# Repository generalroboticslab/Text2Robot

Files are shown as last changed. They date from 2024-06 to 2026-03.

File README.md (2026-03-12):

# Text2Robot

Ryan Ringel,
[Zachary Charlick](https://zacharycharlick.com),
[Jiaxun Liu](https://jiaxunliu.com),
Boxi Xia,
[Boyuan Chen](http://boyuanchen.com/)
<br>
Duke University
<br>

### [Project Website](http://www.generalroboticslab.com/blogs/blog/2024-06-28-text2robot/index.html) | [Video](https://www.youtube.com/watch?v=Cwq7G6OUeGg) | [Paper](https://arxiv.org/abs/2406.19963)

## Overview
This repo contains the Fusion360 and Python implementation for paper "Text2Robot." Our pipeline automatically converts a text prompt to a quadrupedal robot. We utilize a state of the art text to mesh generative model as initialization for our pipeline, and convert the static mesh to a kinetic robot model. We evolve the robots control and morphology simultaneously using our evolutionary algorithm.

<p align="center">
    teaser
</p>

## Citation

If you find our paper or codebase helpful, please consider citing:

```
@article{ringel2024text2robot,
      title={Text2Robot: Evolutionary Robot Design from Text Descriptions}, 
      author={Ryan P. Ringel and Zachary S. Charlick and Jiaxun Liu and Boxi Xia and Boyuan Chen},
      year={2024},
      eprint={2406.19963},
      archivePrefix={arXiv},
      primaryClass={cs.RO},
      url={https://arxiv.org/abs/2406.19963}, 
}
```

## Content

- [Installation](#installation)
- [Text2Mesh](#text2mesh)
- [Mesh2CAD](#mesh2cad)
- [CAD2URDF](#cad2urdf)
- [Evolutionary Loop](#evolutionary-loop)
- [Sim2Real](#sim2real)

## Project Structure
```
├── conda_env_py38.yaml                     # Conda enviornment for isaacgym
├── Assembly Instructions.pdf               # Instructions for print and assembly of bots
├── Evolutionary_Algorithm
│   ├── driver.py                           # Evolutionary algo driver
│   ├── Example_Frog_Experiment             # Example Experiment URDF_Bank and directory
│   ├── experiments                         # Customize command line overrides for your experiment
│   ├── extract_rewards_from_tensorboard_file.py
│   ├── gen_config_file.py
│   ├── greatest_reward.py
│   ├── init_population.py
│   ├── __init__.py
│   ├── output
│   ├── __pycache__
│   ├── swapping.py
│   ├── train_util.py
│   └── util.py
├── Fusion360_Scripts                               
│   ├── Install_Packages                   # Install necessary python packages for Fusion360
│   └── Wrapper                            # Mesh to Robot Model(s) w/ geometric slicing
├── __init__.py
├── legged_env
│   ├── assets
│   ├── envs                               # Navigate here for visualization & sim2real
│   ├── __init__.py
│   ├── __pycache__
│   └── README.md
├── README.md
├── Sim2Real                               # Sim2Real receiver for RaspPi
│   └── receiver.py
└── STL_Files                              # Example Text-to-mesh and modular components
    ├── Electronics_Modules
    └── Example_Meshes
```
## Installation

The installation has been tested on Ubuntu 22.04.4 LTS with CUDA 12.3. The experiments are performed on several different servers with either PNY RTX A6000, NVIDIA GeForce RTX 3090, or NVIDIA A100 PCIe GPUs.

The conda yaml file `conda_env_py38.yaml` can be found in the base folder of the repo

```bash
alias conda="micromamba"

# Create environment
conda env create --file conda_env_py38.yaml -y

# Activate the environment
conda activate py38

# Export library path
export LD_LIBRARY_PATH=${CONDA_PREFIX}/lib
```

For Fusion360 geometric slicing installation, see section [Mesh2CAD](#mesh2cad)

## Text2Mesh
We use the Meshy website https://www.meshy.ai/ to generate STL meshes from text prompts. STL's used in our experiments are provided in `STL_Files/Example_Meshes`. 

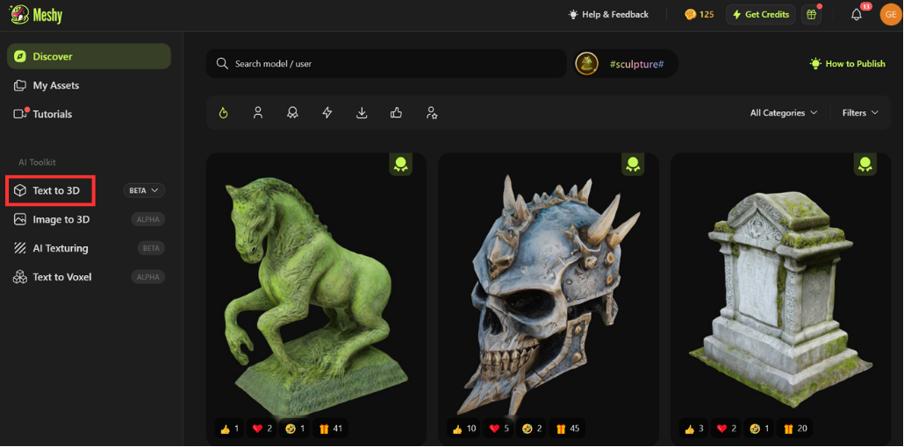
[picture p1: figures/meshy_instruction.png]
MeshyHomeScreen


Additional meshes can be generated using Meshy, although they are not guaranteed to work with the provided slicing script. Include the keywords "quadrupedal walking robot" in the text prompt for best results.

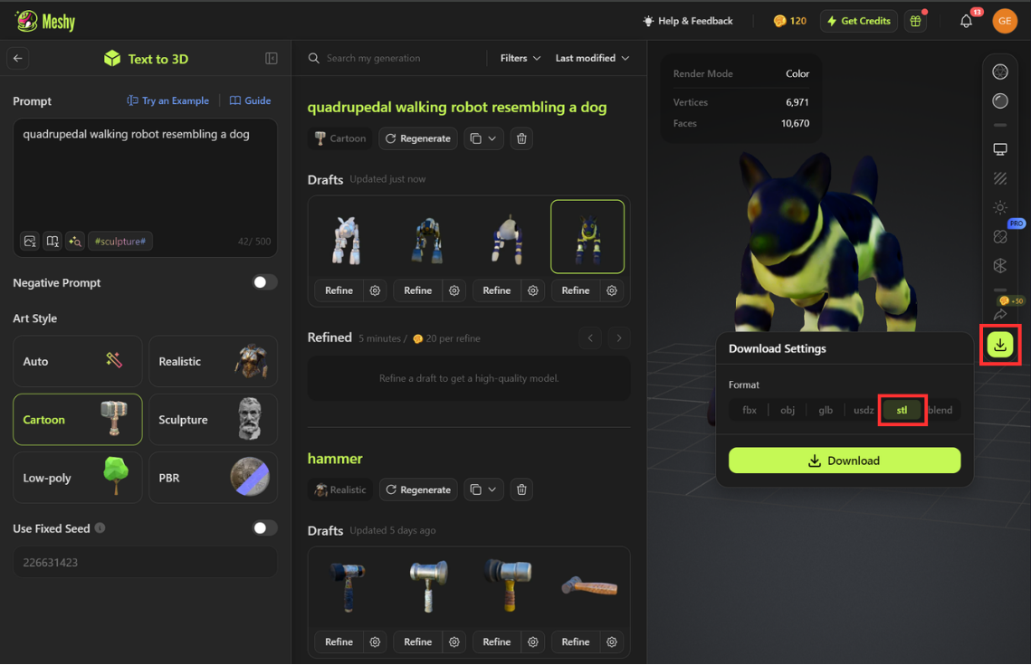
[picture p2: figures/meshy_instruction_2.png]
MeshyText


## Mesh2CAD

STL meshes can be converted to a fusion360 assembly using the provided sliceBody script. First open Fusion360, and preprocess the generated or downloaded mesh desired. Installation instructions can be found at https://www.autodesk.com/campaigns/education/fusion-360. Insert the mesh into a fusion360 document, and use the convert mesh operation to convert the mesh to a brepboy. Organic mesh conversion is enabled with the fusion design extension.

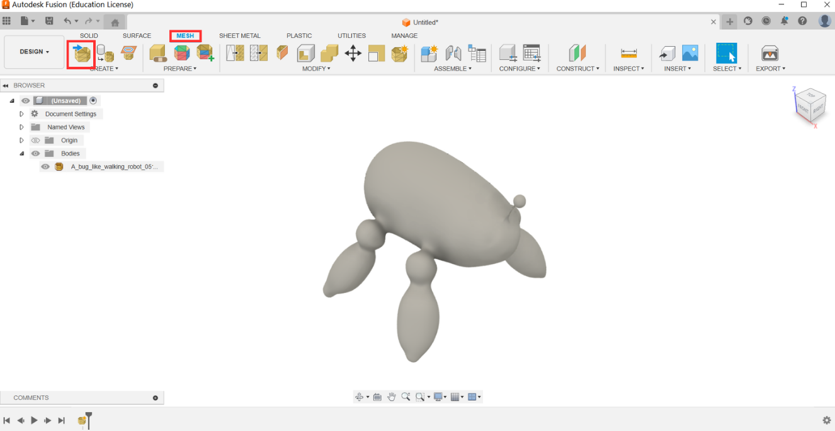
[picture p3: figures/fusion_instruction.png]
InsertMesh

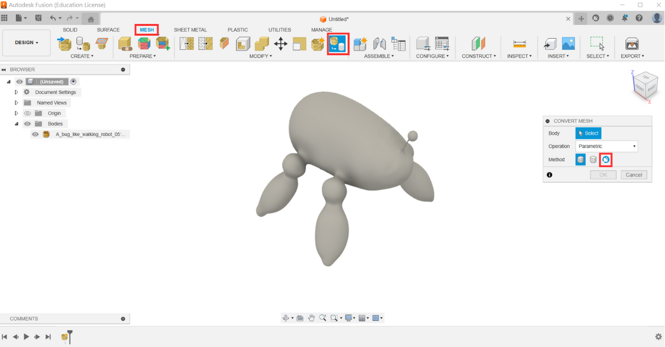
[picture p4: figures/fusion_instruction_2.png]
ConvertMesh


To slice the brepbody, add both python scripts in the 'Fusion360_Scripts' folder into Fusion360. To link an add-in in Fusion360, click on the green plus, and navigate to and select the Wrapper and Install_Packages folders.

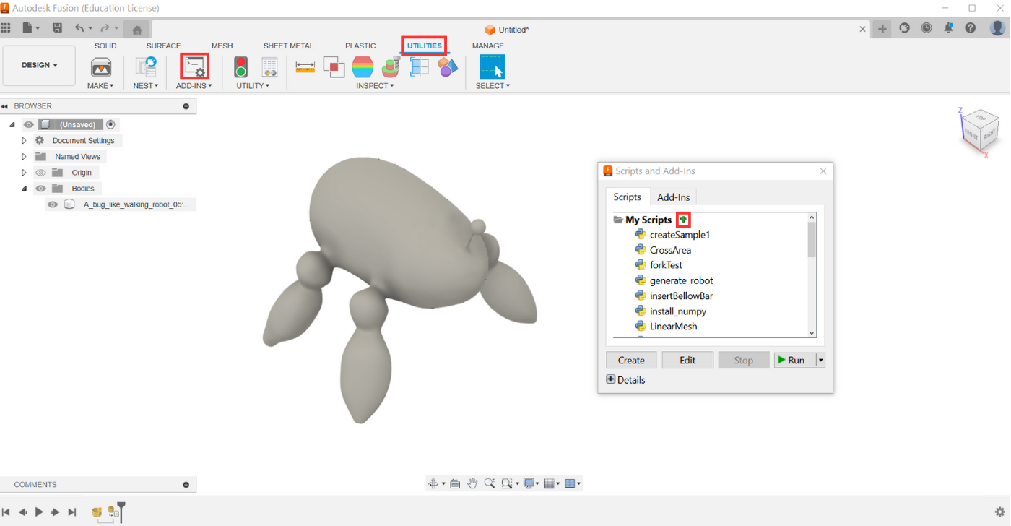
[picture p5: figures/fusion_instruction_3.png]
AddScripts


Prior to running the Wrapper script, add "Polyethylene Low Density" material to favorites by navigating to the fusion material library plastics folder, right clicking on polyethylene low density, and adding to favorites. 

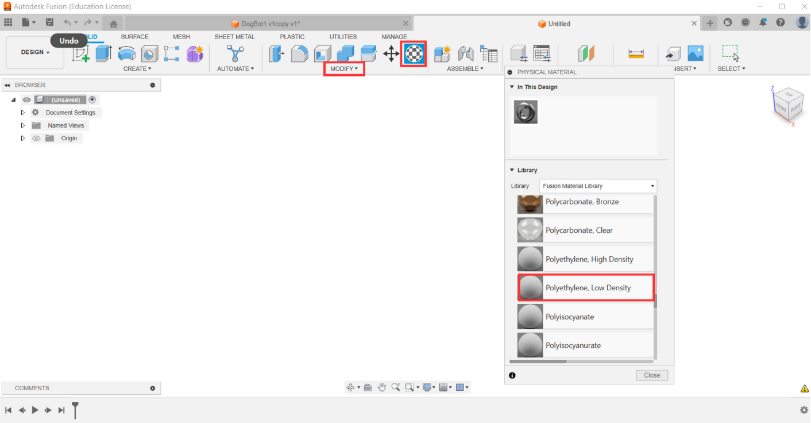
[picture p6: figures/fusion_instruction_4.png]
AddMaterial


Run Install_Packages to install necessary python libraries to the same file path as the wrapper script. Running the Wrapper script will convert the preprocessed brepbody to a robot assembly. If the mesh does not properly slice, adjusting the steps in the slicebyDX function of slicebody can adjust the location of shoulder slices.

AdjustSteps

## CAD2URDF

Uncommenting the URDF exporter function in wrapper will export the generated robot to a URDF. Uncommenting the loop will create 30 variations of the generated robot, and export all as URDF's. This may take up to 15 minutes.

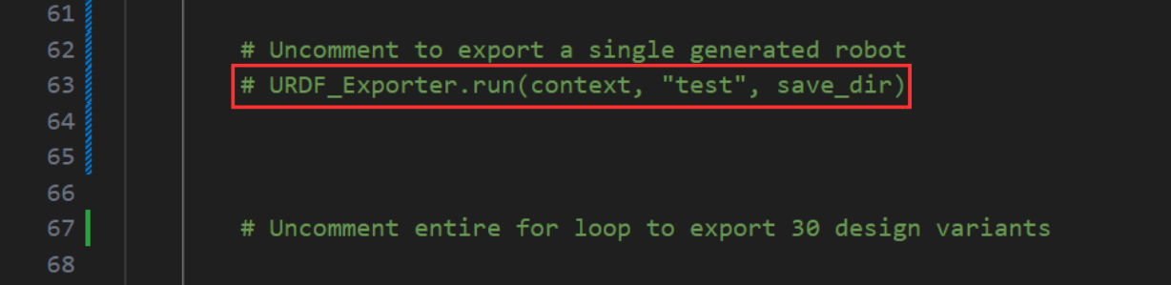
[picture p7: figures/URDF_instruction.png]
URDFExporter

## Evolutionary Loop

To further evolve robots using our evolutionary algorithm, create an experiment directory similar to our provided example: `Evolutionary_Algorithm/Example_Experiment`. If you wish to make custom changes to the training parameters, you can create a configuration file for the experiment in the `Evolutionary_Algorithm/experiments` directory, modeling it after our example. This directory should contain a folder `URDF_Bank`, which will hold the entire gene pool. We recommend using at least 5 prompts for a total of 150 robot models. If you have fewer, you will need to modify `Evolutionary_Algorithm/init_population` to initialize a smaller first generation. You can include as many robots as you would like!

You can run `driver.py` out of the box to train our example Frog experiment! Or, to use your own models, under the `Evolutionary_Algorithm/experiments` folder, duplicate and rename `Example_Frog_Experiment.py`. Change the `robot_names` array to include the names of each prompt in the bank. Ensure the naming convention for your robots is correct. For example, if you have a bank of just one prompt 'Frog' (with 30 total models), each of the 30 models should follow the naming convention: `Frog_Frog_top-z-9_Frog_bottom-z-9.urdf` with 'z' and '9' replaced by the three axis orientations `[x, y, z]`, and all possible limb scales `0-9`.

Lines 20-25 of `driver.py` can be edited to change the number of generations of evolution, as well as preferences for energy efficiency, velocity tracking accuracy, or performance on rough terrain.

```bash
max_generations = 55
inform_based_on_energy = False
inform_based_on_velocity = False
rough_terrain = False
```

You will also need to adjust the GPU configuration settings on `driver.py` line `#67` to match your system properties.

After setting up the experiment, navigate to the `Evolutionary_Algorithm` folder, and run `driver.py`. `driver.py` can be updated to change the max generations of evolution, rough vs flat terrain, and if there should be an additional user specified preference of velocity tracking accuracy, or energy efficiency.

After running the experiment, you can visualize any of the evolved robots and their walking policies. Navigate to `legged_env/envs` and run:
```bash
bash run.sh example -pk
```
to visualize an example checkpoint of an evolved frog. To visualize your own bot, create a new entry in `exp.sh` modeled after `example`. Here you can specify the path to the robot urdf, and the path to the checkpoint file. -pk specifies playback mode, with keyboard input enabled. This will allow you to control the velocity of your robot using (ijkl) as arrow keys and (u and o) to control yaw (rotational velocity). For a full list of playback options, check out `run.sh`. If you run into unexpected errors, make sure you have the conda environment activated!

## Sim2Real

Instructions for printing and assembling your robot can be found in [Assembly Instructions.pdf](Assembly%20Instructions.pdf).

For Sim2Real, download the Sim2Real_Receiver/receiver.py folder on to your robots RaspberryPi. You will also need to initialize the servo python control library found at: https://github.com/ethanlipson/PyLX-16A

Running the receiver.py python script will listen for the UDP message packs that are transmitted when a robot is being played in simulation. You will need to match the target_url of the data receiver and data publisher. The data publisher url can be modified using a command line override to issacgym "task.env.dataPublisher.target_url," and can be specified in the bash profile for playback in `legged_envs/envs/exp.sh`. We provide an example in this file.

```bash
example(){
    base
    task=RobotDog
    PLAY_ARGS+=(
        num_envs=1
        checkpoint=assets/checkpoints/example_frog.pth
    )
    BASE_ARGS+=(
    # task.env.terrain.terrainType=plane
    ++task.env.urdfAsset.root="assets/urdf/example_frog"
    task.env.urdfAsset.file="frog.urdf"
    task.env.randomCommandVelocityRanges.linear_x=[-0.5,0.5]
    task.env.randomCommandVelocityRanges.linear_y=[-0.5,0.5]
    task.env.randomCommandVelocityRanges.yaw=[-1,1]

    task.env.dataPublisher.enable=true
    task.env.dataPublisher.target_url=udp://10.172.14.96:9870
    )
}
```

## License

This repository is released under the Apache License 2.0. See [LICENSE](LICENSE) for additional details.

## Acknowledgement

`This work is supported by DARPA FoundSci program under award HR00112490372, by ARL STRONG program under awards W911NF2320182 and W911NF2220113.`

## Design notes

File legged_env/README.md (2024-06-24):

# project structure
```
.
├── assets
│   ├── checkpoints # saved checkpoint
│   │   ├── A1Terrain.pth
│   │   └── ...
│   ├── joint_monkey.py # script to check the urdf
│   └── urdf
│       ├── a1
│       ├── anymal_c
│       └──...
├── envs
│   ├── cfg # stores all configurations
│   │   ├── config.yaml
│   │   ├── pbt
│   │   ├── task
│   │   └── train
│   ├── common # common scripts
│   │   ├── publisher.py
│   │   ├── terrain.py
│   │   └── utils.py
│   ├── exp.sh # experiment scripts
│   ├── __init__.py
│   ├── plot_juggler # plot_juggler configurations
│   │   └── robotdog7kg_play_debug.xml
│   ├── run.sh # run script
│   ├── setup # conda env setup script
│   │   ├── conda_env.yaml
│   │   └── ...
│   ├── tasks # 
│   │   ├── __init__.py
│   │   └── legged_terrain.py
│   └── train.py
├── outputs # contains trained results
└── README.md
```

# to run example:

```bash
cd envs
# robot dog7kg
bash run.sh dog -p
# a1
bash run.sh a1Terrain -p
# anymal
bash run.sh anymalTerrain -p
```

# to start conda env
```
conda activate py38 && export LD_LIBRARY_PATH=${CONDA_PREFIX}/lib
```

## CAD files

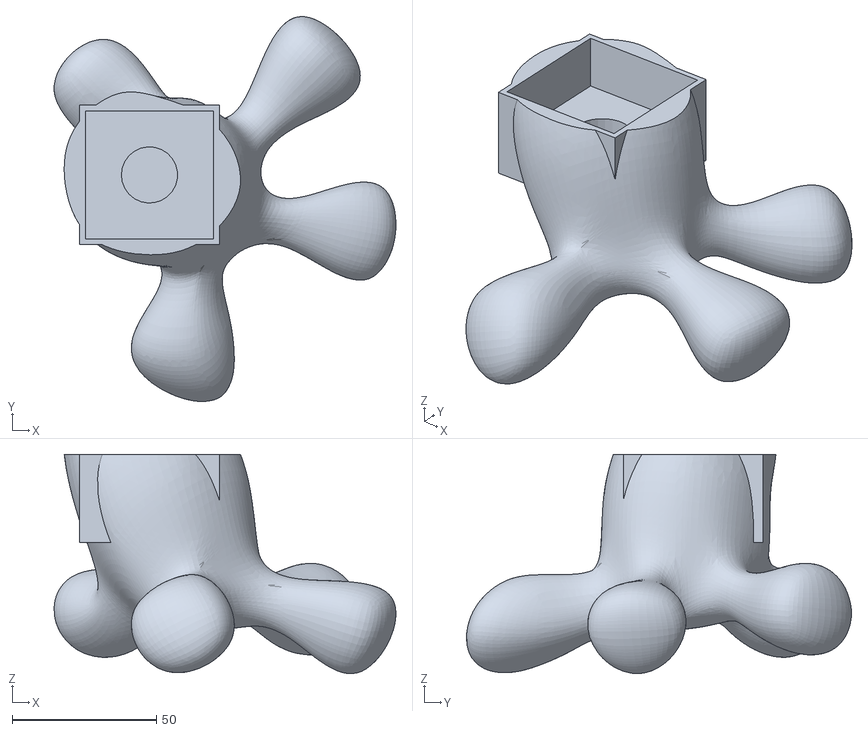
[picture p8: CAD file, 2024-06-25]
Evolutionary_Algorithm/Example_Frog_Experiment/URDF_Bank/FrogBot1_FrogBot1_top-x-0_FrogBot1_bottom-x-0/simple_meshes/body_2_2_1.stl
118.6 x 133.5 x 76.0

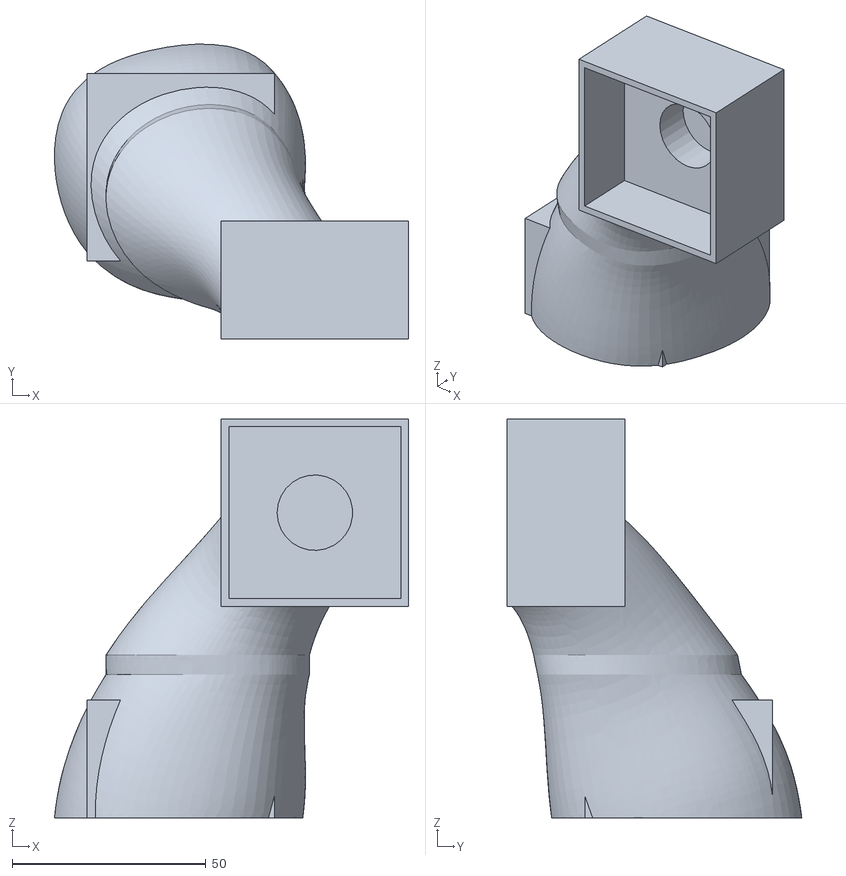
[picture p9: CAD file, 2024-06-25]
Evolutionary_Algorithm/Example_Frog_Experiment/URDF_Bank/FrogBot1_FrogBot1_top-x-1_FrogBot1_bottom-x-1/simple_meshes/body_1_1_1.stl
91.5 x 76.1 x 103.1

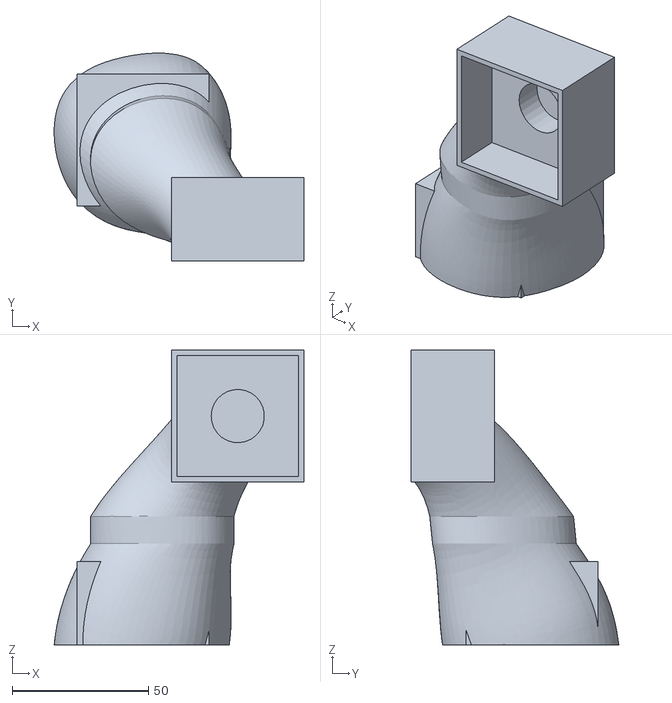
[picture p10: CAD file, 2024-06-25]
Evolutionary_Algorithm/Example_Frog_Experiment/URDF_Bank/FrogBot1_FrogBot1_top-x-2_FrogBot1_bottom-x-2/simple_meshes/body_1_1_1.stl
91.5 x 76.1 x 108.1

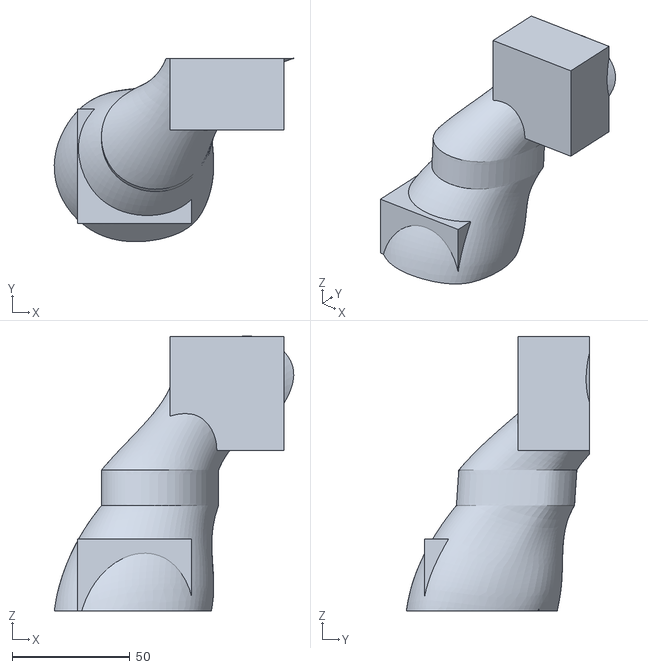
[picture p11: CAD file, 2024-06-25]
Evolutionary_Algorithm/Example_Frog_Experiment/URDF_Bank/FrogBot1_FrogBot1_top-x-3_FrogBot1_bottom-x-3/simple_meshes/body_1_3_1.stl
101.6 x 77.8 x 116.6

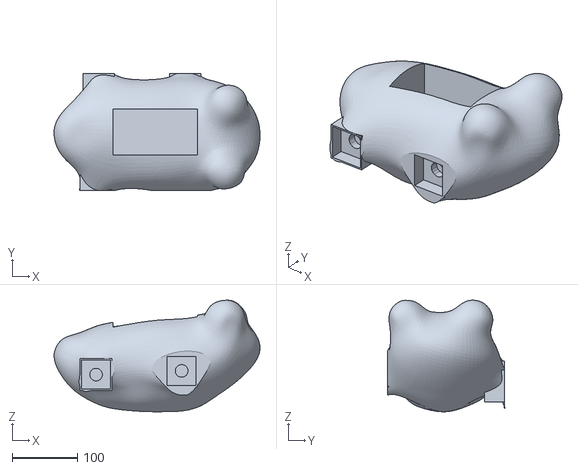
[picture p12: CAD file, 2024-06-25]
Evolutionary_Algorithm/Example_Frog_Experiment/URDF_Bank/FrogBot1_FrogBot1_top-x-4_FrogBot1_bottom-x-4/simple_meshes/base_link.stl
314.6 x 179.2 x 170.5

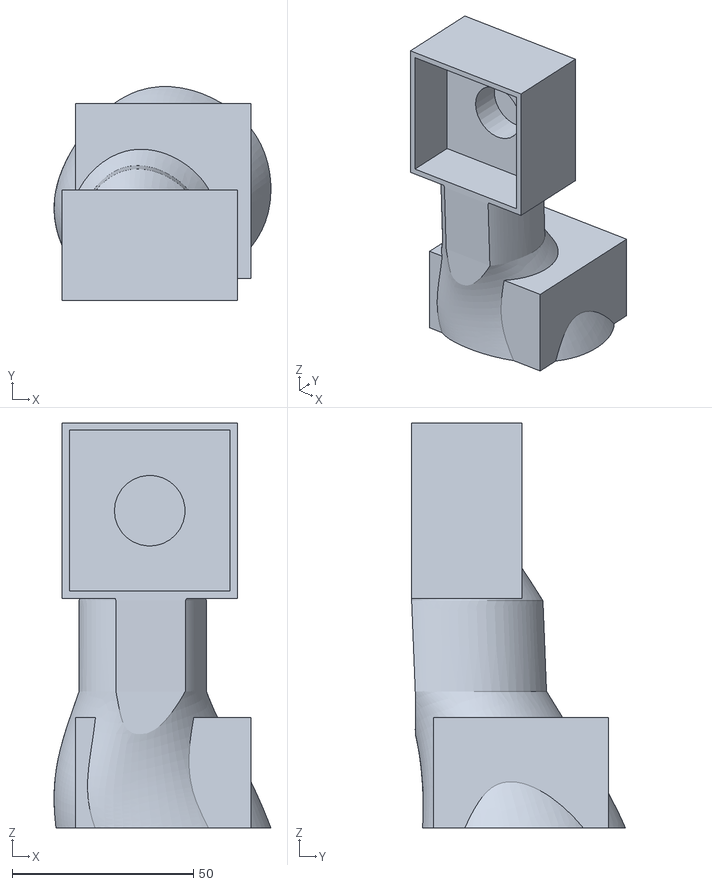
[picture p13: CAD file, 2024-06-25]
Evolutionary_Algorithm/Example_Frog_Experiment/URDF_Bank/FrogBot1_FrogBot1_top-x-5_FrogBot1_bottom-x-5/simple_meshes/body_1_0_1.stl
59.8 x 59.0 x 111.7

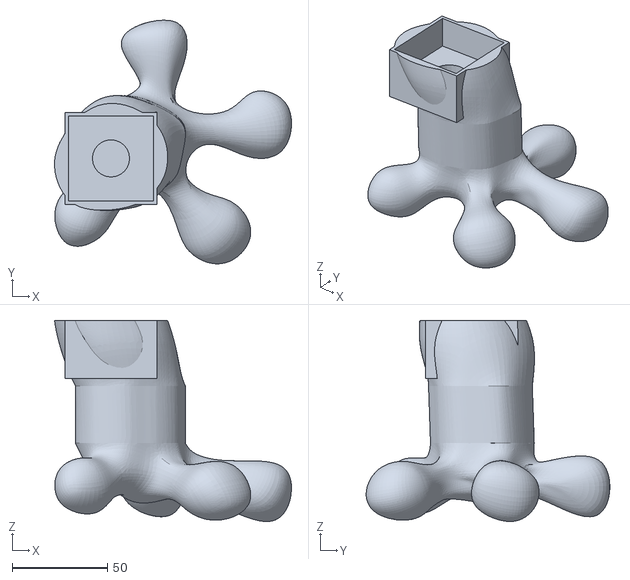
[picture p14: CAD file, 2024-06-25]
Evolutionary_Algorithm/Example_Frog_Experiment/URDF_Bank/FrogBot1_FrogBot1_top-x-6_FrogBot1_bottom-x-6/simple_meshes/body_2_0_1.stl
124.3 x 127.8 x 105.4

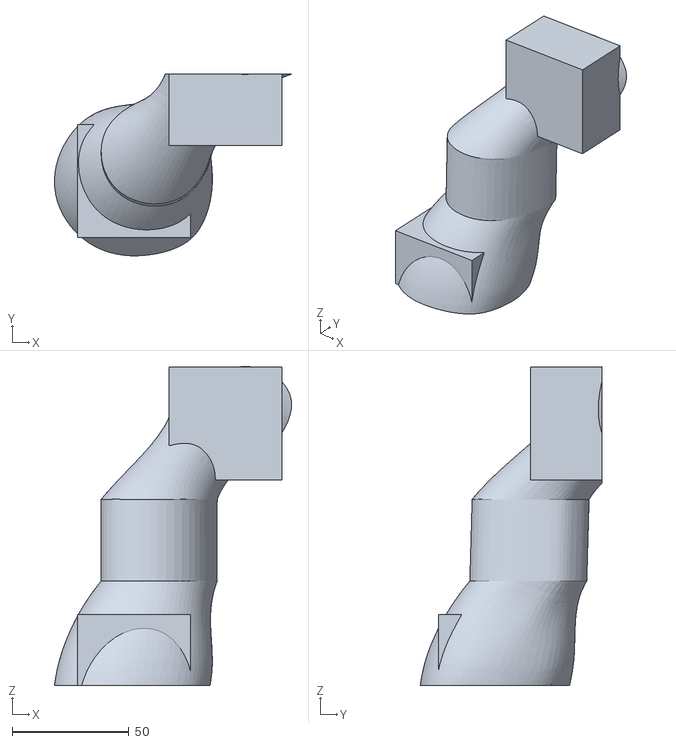
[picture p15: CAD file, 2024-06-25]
Evolutionary_Algorithm/Example_Frog_Experiment/URDF_Bank/FrogBot1_FrogBot1_top-x-7_FrogBot1_bottom-x-7/simple_meshes/body_1_3_1.stl
101.6 x 77.8 x 136.6

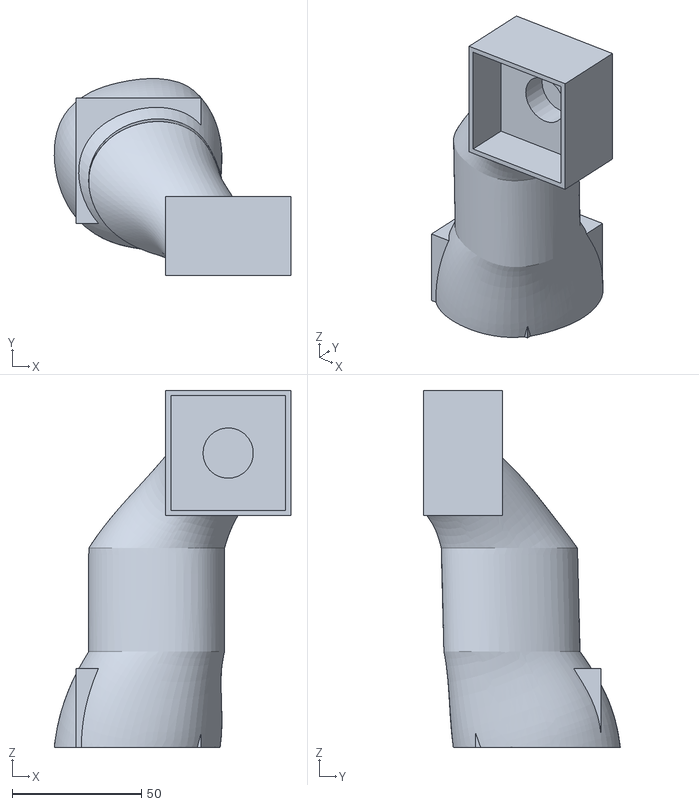
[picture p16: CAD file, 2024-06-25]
Evolutionary_Algorithm/Example_Frog_Experiment/URDF_Bank/FrogBot1_FrogBot1_top-x-8_FrogBot1_bottom-x-8/simple_meshes/body_1_1_1.stl
91.5 x 76.1 x 138.1

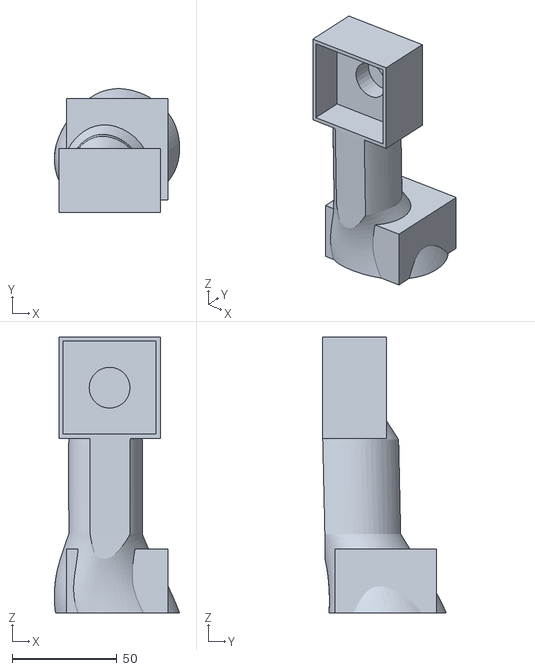
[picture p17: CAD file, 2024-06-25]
Evolutionary_Algorithm/Example_Frog_Experiment/URDF_Bank/FrogBot1_FrogBot1_top-x-9_FrogBot1_bottom-x-9/simple_meshes/body_1_0_1.stl
59.8 x 59.0 x 131.7

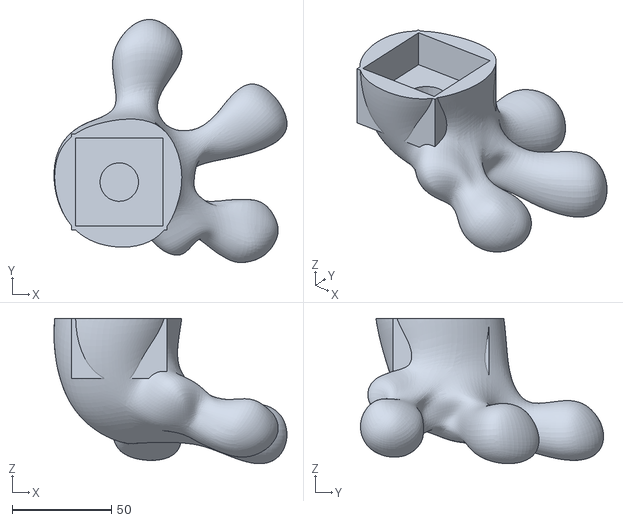
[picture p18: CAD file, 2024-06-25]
Evolutionary_Algorithm/Example_Frog_Experiment/URDF_Bank/FrogBot1_FrogBot1_top-y-0_FrogBot1_bottom-y-0/simple_meshes/body_2_1_1.stl
117.6 x 122.8 x 73.4

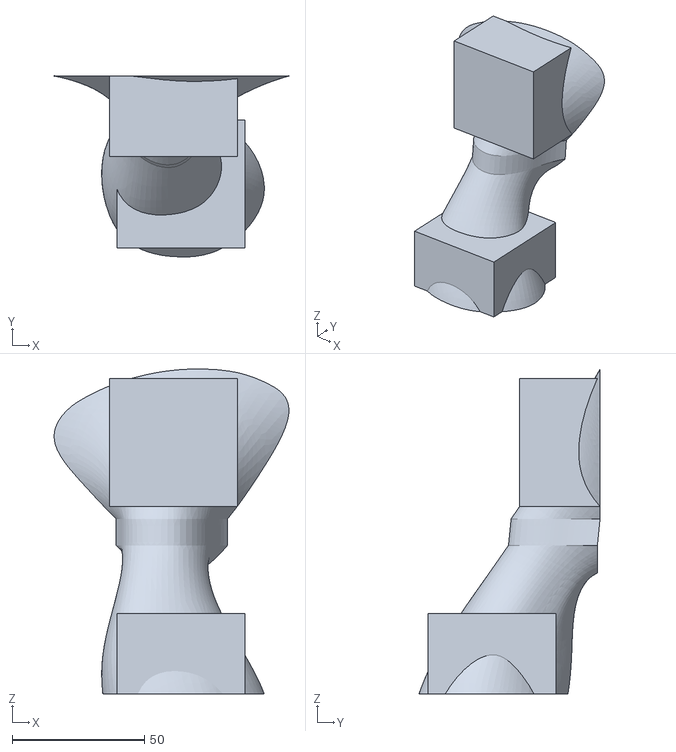
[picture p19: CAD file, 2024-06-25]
Evolutionary_Algorithm/Example_Frog_Experiment/URDF_Bank/FrogBot1_FrogBot1_top-y-2_FrogBot1_bottom-y-2/simple_meshes/body_1_2_1.stl
88.9 x 68.6 x 123.1

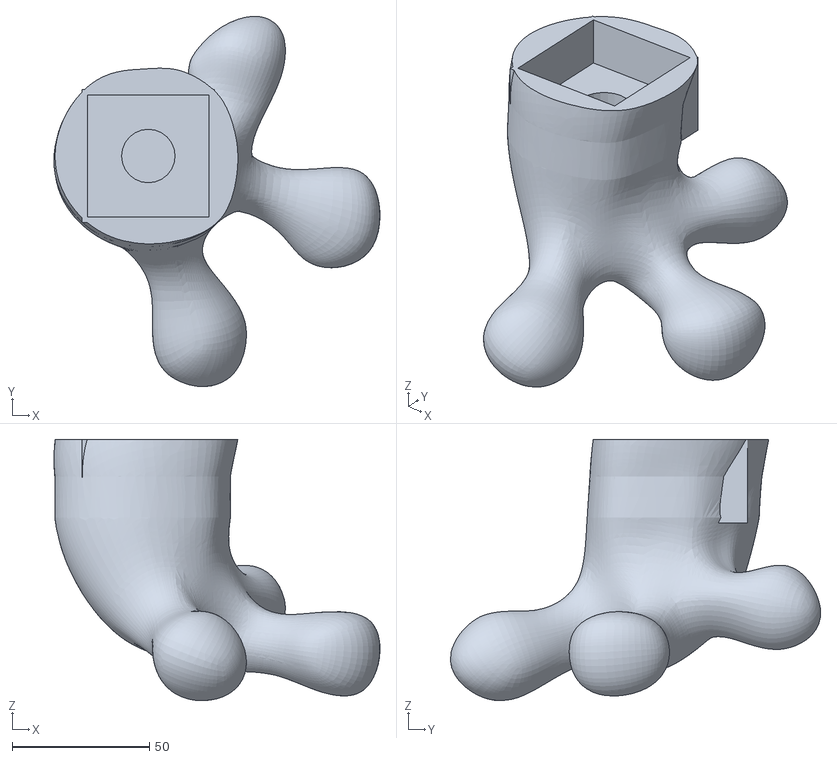
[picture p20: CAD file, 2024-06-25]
Evolutionary_Algorithm/Example_Frog_Experiment/URDF_Bank/FrogBot1_FrogBot1_top-y-3_FrogBot1_bottom-y-3/simple_meshes/body_2_3_1.stl
118.8 x 134.9 x 95.2

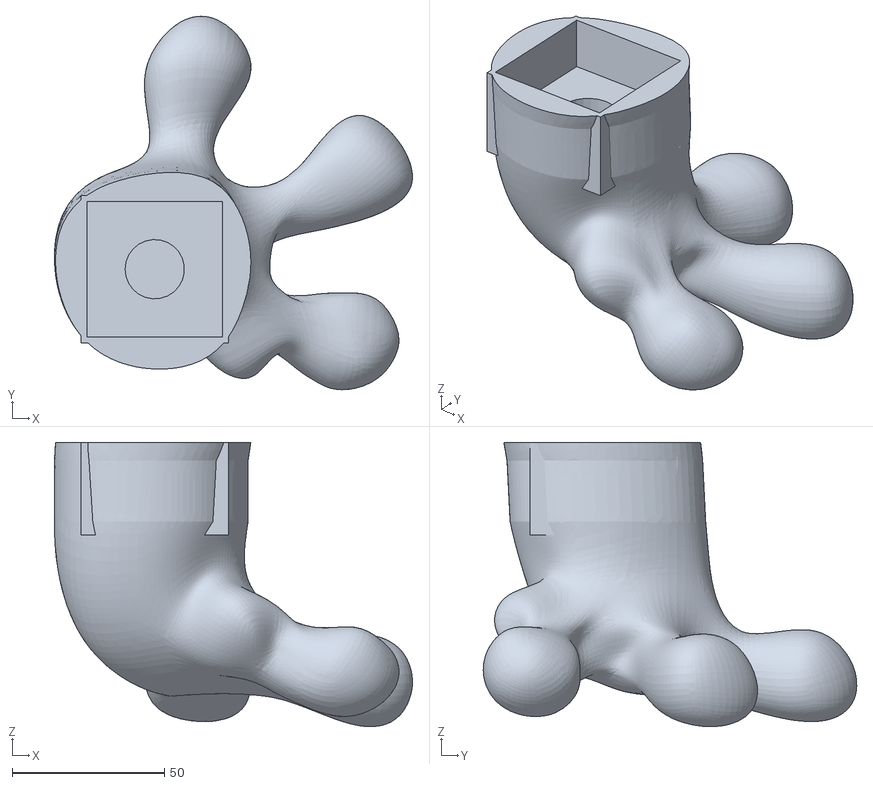
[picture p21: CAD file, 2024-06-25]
Evolutionary_Algorithm/Example_Frog_Experiment/URDF_Bank/FrogBot1_FrogBot1_top-y-4_FrogBot1_bottom-y-4/simple_meshes/body_2_1_1.stl
117.6 x 122.8 x 93.4

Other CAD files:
Evolutionary_Algorithm/Example_Frog_Experiment/URDF_Bank/FrogBot1_FrogBot1_top-y-5_FrogBot1_bottom-y-5/simple_meshes/body_1_2_1.stl
Evolutionary_Algorithm/Example_Frog_Experiment/URDF_Bank/FrogBot1_FrogBot1_top-y-6_FrogBot1_bottom-y-6/simple_meshes/body_2_3_1.stl
Evolutionary_Algorithm/Example_Frog_Experiment/URDF_Bank/FrogBot1_FrogBot1_top-y-7_FrogBot1_bottom-y-7/simple_meshes/body_1_1_1.stl
Evolutionary_Algorithm/Example_Frog_Experiment/URDF_Bank/FrogBot1_FrogBot1_top-x-0_FrogBot1_bottom-x-0/simple_meshes/base_link.stl
Evolutionary_Algorithm/Example_Frog_Experiment/URDF_Bank/FrogBot1_FrogBot1_top-x-0_FrogBot1_bottom-x-0/simple_meshes/body_1_0_1.stl
Evolutionary_Algorithm/Example_Frog_Experiment/URDF_Bank/FrogBot1_FrogBot1_top-x-0_FrogBot1_bottom-x-0/simple_meshes/body_1_1_1.stl
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

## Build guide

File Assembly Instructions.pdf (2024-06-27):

### Assembly Instructions - Text2Robot

Hardware

Item / Link | Quantity
Microcontroller Raspberry Pi 4 Model B (https://www.amazon.com/Raspberry-Model-2019-Quad-Bluetooth/dp/B07TC2BK1X) | 1
Battery Povway 5200 mA Lipo 3S 11.1V 50C (https://www.amazon.com/POVWAY-2200mAh-Compatible-Airplane-Helicopter/dp/B07XKWM8PP) | 1
Servo Motor Hiwonder HT D − 45H High Voltage Serial Bus Servo 45 KG (https://www.amazon.com/Hiwonder-HTD-45H-Voltage-Connectors-Feedback/dp/B0CB3T1P7Y) | 8
DC to DC Power Converter DROK 10A Synchronous Step-Down Voltage Regulator DC-DC (https://www.amazon.com/DROK-Synchronous-Step-Down-Continuously-Adjustable/dp/B00BYS9JYA?hvadid=693071814379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) | 1
PLA Filament Ender PLA 3D Printer PLA Filament 1.75 mm 1KG (2.2 lbs) Spool PLA White (https://www.amazon.com/Creality-Filament-1KG-Diameter-Accuracy-Filament/dp/B0B5QN34XT?s=industrial) | 1
Motor Controller Hiwonder TTL / USB Debugging Board (https://www.amazon.com/LewanSoul-BusLinker-Debug-Board-LX-16A/dp/B073WRLJB2?hvadid=693442482467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) | 1
LiPo Battery Connector Adapter (https://www.amazon.com/YLP-Battery-Connector-Compatible-Connectors/dp/B088WLS9J1?s=electronics) | 1
USB C Cable 3A Fast Charge, USB A to Type C (https://www.amazon.com/Charging-etguuds-Charger-Compatible-Samsung/dp/B089DM4KDW?s=electronics) | 1

12-14 Gauge Wire

Equipment & Software

Item / Link

Any slicing software (We used Creality Slicer) (https://www.creality.com/pages/download-software)

Soldering Iron, Solder, Wirestrippers

Access to a 3D Printer (We used a Creality Ender 3) (https://www.amazon.com/Creality-Ender-3-High-Precision-High-standard-V-profile/dp/B07D218NX3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)

https://github.com/ethanlipson/PyLX-16A

### Assembly Instructions

### 1. Slice and Print STL Files

- Slice and print every STL file referenced by the selected robot’s URDF. This includes one baselink (main body), 4 upper legs, and 4 lower legs. Depending on your printer bed size, you may need to split and splice some parts using strong super glue.

### 2. Download and Print Electronics Modules

- Download the STL files in the STL_Files/Electronics_Modules folder.
- Slice and print 4 KneeConnectors, 12 MotorCases, and one BatteryBox.

### 3. Assemble Components

- Snap together the MotorCases, KneeConnectors, and printed robot limbs according to the URDF. Attach the KneeConnectors directly to each foot, following the specified axis orientations.
- Daisy chain the two servos on each leg together and connect the topmost servo to the Hiwonder Debugging Board.

### 4. Prepare Wiring

- Cut four 1-foot strips of additional wire. Solder the ground and power of the battery connector adapter into a Y-configuration.
- Use heat shrink tubing to group together one set of terminals for the Raspberry Pi and one set for the servo board.
- Connect one Y directly to the ground and power of the servo board. Do not connect the Raspberry Pi directly to the battery as it is only rated for 5V.
- Connect the second Y to the input of the DC-to-DC power converter. Adjust the potentiometer until the output voltage is 5V with the input battery voltage (11.1V). Carefully check the output voltage with a multimeter to avoid frying the Raspberry Pi.

### 5. Connect Power to Raspberry Pi

- Cut off the USB-A end of the USBC-to-USB charging cable. Connect the ground and power wires to the outputs of the DC-to-DC power converter.
- Plug the USB-C terminal into the Raspberry Pi power. See Figure 1 for the final soldered connector.

### 6. Final Assembly

- Screw the Raspberry Pi, Debugging Board, and DC-to-DC step-down into their respective housings in the BatteryBox. Place the battery into its housing.

### Initialization

### 1. Set Up SSH Communication

- Establish SSH communication with your Raspberry Pi.
- Install the PyLX-16A repository, (https://github.com/ethanlipson/PyLX-16A) which enables remote control of the robot’s servos.

### 2. Center the Servos

- Run the servo-test.py script to center each servo at 120 degrees, the default position specified by the URDF.
- Set servo limits to avoid harmful self-collision.

### 3. Replay Trained Locomotion Policy

- Refer to the Sim2Real documentation in the ReadMe file to replay the trained locomotion policy on your assembled robot.

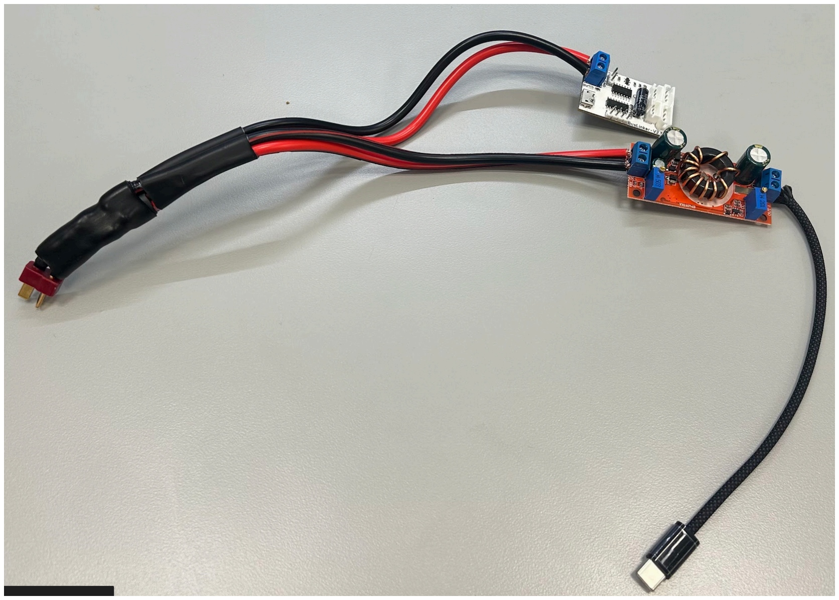
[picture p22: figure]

Figure 1: Soldered T-Connector to two Ys. One powers the servo board, one connects to the DC step down, and then to the RaspberryPi

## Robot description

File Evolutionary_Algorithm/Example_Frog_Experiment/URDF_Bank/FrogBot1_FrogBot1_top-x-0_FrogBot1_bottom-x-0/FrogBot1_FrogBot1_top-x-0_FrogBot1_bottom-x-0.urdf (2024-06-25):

<?xml version="1.0" ?>
<robot name="FrogBot1_top-FrogBot1-x-0_bottom-FrogBot1-x-0">

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

<link name="base_link">
  <inertial>
    <origin xyz="0 0 0" rpy="0 0 0"/>
    <mass value="1.4004497258118793"/>
    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
  </inertial>
  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
</link>

<link name="body_1_0_1">
  <inertial>
    <origin xyz="-0.045735 -0.109621 -0.00462" rpy="0 0 0"/>
    <mass value="0.02985675796874187"/>
    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
  </inertial>
  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
</link>

<link name="body_1_1_1">
  <inertial>
    <origin xyz="0.086489 -0.109621 -0.018802" rpy="0 0 0"/>
    <mass value="0.053275121493263654"/>
    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
  </inertial>
  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
</link>

<link name="body_1_2_1">
  <inertial>
    <origin xyz="-0.040267 0.109621 -0.027764" rpy="0 0 0"/>
    <mass value="0.0417219417099986"/>
    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
  </inertial>
  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
</link>

<link name="body_1_3_1">
  <inertial>
    <origin xyz="0.090407 0.109621 -0.022193" rpy="0 0 0"/>
    <mass value="0.05617496746494577"/>
    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
  </inertial>
  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
</link>

<link name="body_2_0_1">
  <inertial>
    <origin xyz="-0.049562 -0.158797 0.075064" rpy="0 0 0"/>
    <mass value="0.08251740555525651"/>
    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
  </inertial>
  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
</link>

<link name="body_2_1_1">
  <inertial>
    <origin xyz="0.121182 -0.172952 0.075064" rpy="0 0 0"/>
    <mass value="0.08523650293632644"/>
    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
  </inertial>
  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
</link>

<link name="body_2_2_1">
  <inertial>
    <origin xyz="-0.04311 0.169506 0.075064" rpy="0 0 0"/>
    <mass value="0.08378108136187434"/>
    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
  </inertial>
  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
</link>

<link name="body_2_3_1">
  <inertial>
    <origin xyz="0.129712 0.174384 0.075064" rpy="0 0 0"/>
    <mass value="0.08379398246620173"/>
    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
  </inertial>
  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
</link>

<joint name="joint_1_0" type="revolute">
  <origin xyz="0.045735 0.109621 0.00462" rpy="0 0 0"/>
  <parent link="base_link"/>
  <child link="body_1_0_1"/>
  <axis xyz="1.0 0.0 0.0"/>
  <limit upper="1.2" lower="-1.2" effort="3.8" velocity="5.4"/>
</joint>
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

<joint name="joint_1_1" type="revolute">
  <origin xyz="-0.086489 0.109621 0.018802" rpy="0 0 0"/>
  <parent link="base_link"/>
  <child link="body_1_1_1"/>
  <axis xyz="1.0 0.0 0.0"/>
  <limit upper="1.2" lower="-1.2" effort="3.8" velocity="5.4"/>
</joint>
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

<joint name="joint_1_2" type="revolute">
  <origin xyz="0.040267 -0.109621 0.027764" rpy="0 0 0"/>
  <parent link="base_link"/>
  <child link="body_1_2_1"/>
  <axis xyz="1.0 0.0 0.0"/>
  <limit upper="1.2" lower="-1.2" effort="3.8" velocity="5.4"/>
</joint>
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

<joint name="joint_1_3" type="revolute">
  <origin xyz="-0.090407 -0.109621 0.022193" rpy="0 0 0"/>
  <parent link="base_link"/>
  <child link="body_1_3_1"/>
  <axis xyz="1.0 0.0 0.0"/>
  <limit upper="1.2" lower="-1.2" effort="3.8" velocity="5.4"/>
</joint>
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

<joint name="joint_2_0" type="revolute">
  <origin xyz="0.003827 0.049176 -0.079684" rpy="0 0 0"/>
  <parent link="body_1_0_1"/>
  <child link="body_2_0_1"/>
  <axis xyz="1.0 0.0 0.0"/>
  <limit upper="1.2" lower="-1.2" effort="3.8" velocity="5.4"/>
</joint>
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

<joint name="joint_2_1" type="revolute">
  <origin xyz="-0.034693 0.063331 -0.093866" rpy="0 0 0"/>
  <parent link="body_1_1_1"/>
  <child link="body_2_1_1"/>
  <axis xyz="1.0 0.0 0.0"/>
  <limit upper="1.2" lower="-1.2" effort="3.8" velocity="5.4"/>
</joint>
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

<joint name="joint_2_2" type="revolute">
  <origin xyz="0.002843 -0.059885 -0.102828" rpy="0 0 0"/>
  <parent link="body_1_2_1"/>
  <child link="body_2_2_1"/>
  <axis xyz="1.0 0.0 0.0"/>
  <limit upper="1.2" lower="-1.2" effort="3.8" velocity="5.4"/>
</joint>
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

<joint name="joint_2_3" type="revolute">
  <origin xyz="-0.039305 -0.064763 -0.097257" rpy="0 0 0"/>
  <parent link="body_1_3_1"/>
  <child link="body_2_3_1"/>
  <axis xyz="1.0 0.0 0.0"/>
  <limit upper="1.2" lower="-1.2" effort="3.8" velocity="5.4"/>
</joint>
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

</robot>

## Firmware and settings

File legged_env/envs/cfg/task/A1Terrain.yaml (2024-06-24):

# used to create the object
name: A1Terrain

physics_engine: 'physx'

env:
  numEnvs: ${resolve_default:4096,${...num_envs}}
  numObservations: "infer" #49 #165 #188
  numActions: 12
  envSpacing: 3.  # [m]
  enableDebugVis: false

  dataPublisher:
    enable: false
    target_url: 'udp://localhost:9870'

  observationNames:
    - linearVelocity
    - angularVelocity
    - projectedGravity
    - commands
    - dofPosition
    - dofVelocity
    - heightMap
    - actions

  terrain:
    terrainType: trimesh # {none, plane, trimesh,heightfield}
    staticFriction: 1.0  # [-]
    dynamicFriction: 1.0  # [-]
    restitution: 0.        # [-]
    # rough terrain only:
    curriculum: True
    mapLength: 10.
    mapWidth: 10.
    numLevels: 10
    maxInitMapLevel: 0
    difficultySale: 1.0 # multiplier for terrain height
    numTerrains: 20
    # terrain types: [smooth slope, rough slope, stairs up, stairs down, discrete, stepping stone]
    terrainProportions: [0.2, 0.2, 0.2, 0.2, 0.2, 0]
    stair: # stairs up/down terrain
      width: 0.31
      height: 0.18
    uniform: # uniform terrain
      height: 0.15
      step: 0.005
    platformSize: 2.0 # [m]
    horizontalScale: 0.1
    verticalScale: 0.001
    borderSize: 25
    slope: 0.4 # corresponds to 20deg slope (tan(20deg) = 0.4)
    # tri mesh only:
    slopeTreshold: 0.5

  baseInitState:
    pos: [0.0, 0.0, 0.4] # x,y,z [m]
    rot: [0.0, 0.0, 0.0, 1.0] # x,y,z,w [quat]
    vLinear: [0.0, 0.0, 0.0]  # x,y,z [m/s]
    vAngular: [0.0, 0.0, 0.0]  # x,y,z [rad/s]
  
  baseHeightTarget: # 0.3 # target base height [m]

  randomCommandVelocityRanges:
    # train
    linear_x: [-1., 1.] # min max [m/s]
    linear_y: [-1., 1.]   # min max [m/s]
    yaw: [-3.14, 3.14]    # min max [rad] yaw angle dirvergence
  commandZeroThreshold: 0.05 # [m/s] treat commends below this threshold as zero

  control:
    # PD Drive parameters:
    stiffness: 40.0  # [N*m/rad]
    damping: 1.0     # [N*m*s/rad]
    limit: 33        # [N*m]
    # action scale: target angle = actionScale * action + defaultAngle
    actionScale: 0.5
    # decimation: Number of control action updates @ sim DT per policy DT
    decimation: 4
  # controlFrequencyInv: 1 # Number of control action updates @ sim DT per policy DT

  defaultJointPositions:  # = target angles when action = 0.0 (in rad)
    FL_hip_joint:  0.1     # [rad]
    RL_hip_joint:  0.1     # [rad]
    FR_hip_joint: -0.1     # [rad]
    RR_hip_joint: -0.1     # [rad]

    FL_thigh_joint: 0.8    # [rad]
    RL_thigh_joint: 1.0    # [rad]
    FR_thigh_joint: 0.8    # [rad]
    RR_thigh_joint: 1.0    # [rad]

    FL_calf_joint: -1.5    # [rad]
    RL_calf_joint: -1.5    # [rad]
    FR_calf_joint: -1.5    # [rad]
    RR_calf_joint: -1.5    # [rad]

  # desiredJointPositions:
  #   FL_hip_joint:  0.1     # [rad]
  #   RL_hip_joint:  0.1     # [rad]
  #   FR_hip_joint: -0.1     # [rad]
  #   RR_hip_joint: -0.1     # [rad]

  #   FL_thigh_joint: 0.8    # [rad]
  #   RL_thigh_joint: 1.0    # [rad]
  #   FR_thigh_joint: 0.8    # [rad]
  #   RR_thigh_joint: 1.0    # [rad]

    # FL_calf_joint: -1.5    # [rad]
    # RL_calf_joint: -1.5    # [rad]
    # FR_calf_joint: -1.5    # [rad]
    # RR_calf_joint: -1.5    # [rad]

  urdfAsset:
    collision_filter: 0
    AssetOptions:
      collapse_fixed_joints: false
      fix_base_link: false
      default_dof_drive_mode: 3 # see DofDriveMode (0: DOF_MODE_NONE, 1: DOF_MODE_POS, 2: DOF_MODE_VEL, 3: DOF_MODE_EFFORT)
      flip_visual_attachments: false
      replace_cylinder_with_capsule: true
    # root: "" # override defualt asset_root
    file: "urdf/a1/a1_minimum.urdf"
    # Body
    # baseName: base
    # hipName: hip
    ## calf if collapsing fixed joint, foot otherwise
    kneeName: calf
    footName: foot 
    # kneeName: thigh
    # footName: calf # calf if collapsing fixed joint, foot otherwise
    # collapse_fixed_joints: True
    ## joint
    # hipJointName: hip
  assetDofProperties: # set_actor_dof_properties (override)
    damping: 0.5

  heightmap:
    x: "${linspace: -0.6, 0.6, 13}"
    y: "${linspace: -0.4, 0.4, 9}"
  
  randomize:
    friction:
      enable: true
      range: [0.5, 1.25]
    baseMass:
      enable: false
      range: [-0.5, 0.5]
    push:
      enable: true
      interval_s: 15
      velMin: [-1,-1, 0, 0, 0, 0]
      velMax: [ 1, 1, 0, 0, 0, 0]
    initDofPos: # randomize dof position at reset
      enable: true
      range: [-0.1, 0.1]
    initDofVel: # randomize dof velocity at reset
      enable: true
      range: [-0.1, 0.1]
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

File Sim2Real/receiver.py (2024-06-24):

import socket
import urllib.parse
import orjson
import msgpack
import torch
import numpy as np
import select
import threading
import subprocess
from pylx16a.lx16a import *
import time
import numpy as np
LX16A.initialize("/dev/ttyUSB0", 0.1) # Change port based on which port is connected to the servo controller

try:
    servo0 = LX16A(0)  # Ensure that real servos match isaacgym indecies, or realign here
    servo1 = LX16A(4)
    servo2 = LX16A(1)
    servo3 = LX16A(5)
    servo4 = LX16A(2)
    servo5 = LX16A(6)
    servo6 = LX16A(3)
    servo7 = LX16A(7)
    servo0.set_angle_limits(0, 240)  # Set safe limits for servos
    servo1.set_angle_limits(0, 240)
    servo2.set_angle_limits(0, 240)
    servo3.set_angle_limits(0, 240)
    servo4.set_angle_limits(0, 240)
    servo5.set_angle_limits(0, 240)
    servo6.set_angle_limits(0, 240)
    servo7.set_angle_limits(0, 240)

except ServoTimeoutError as e:
    print(f"Servo {e.id_} is not responding. Exiting...")
    quit()

class DataPublisher:
    """
    Manages data publishing to a specified target URL.

    Methods
    -------
    publish(data: dict)
        Sends data to the target URL if publishing is enabled.
    """

    SUPPORTED_SCHEMES = {'unix', 'tcp', 'udp'}

    def __init__(
        self,
        target_url: str = 'udp://localhost:9870',
        encoding_type: str = 'msgpack',
        is_broadcast: bool = False,
        is_enabled: bool = True,
        **socket_kwargs,
    ):
        """
        Initialize DataPublisher with connection and encoding details.

        Parameters
        ----------
        target_url : str
            URL to which data will be sent.
        encoding_type : str
            Encoding for sending data, default is 'json'.
        is_broadcast : bool
            If True, data is broadcasted; defaults to True.
        is_enabled : bool
            If False, publishing is inactive; defaults to False.
        socket_kwargs : 
            Additional keyword arguments for the socket.
        """
        self.is_enabled = is_enabled
        self.url = urllib.parse.urlparse(target_url)

        # Validate scheme
        if self.url.scheme not in self.SUPPORTED_SCHEMES:
            raise ValueError(f"Unsupported scheme in URL: {target_url}")

        # Set socket family and type
        family = self._get_socket_family()
        socket_type = socket.SOCK_DGRAM if 'udp' in self.url.scheme else socket.SOCK_STREAM

        # Create socket
        self.socket = socket.socket(family, socket_type, **socket_kwargs)
        if is_broadcast:
            self.socket.setsockopt(socket.SOL_SOCKET, socket.SO_BROADCAST, 1)
        self.hostname = '<broadcast>' if is_broadcast else self.url.hostname

        # Set encoding function
        self._setup_encoding(encoding_type)

    def _get_socket_family(self):
        """Determine and return the appropriate socket family based on the URL."""
        if 'unix' in self.url.scheme:
            return socket.AF_UNIX
        return socket.AF_INET6 if ':' in (self.url.hostname or '') else socket.AF_INET

    def _setup_encoding(self, encoding_type):
        """Configure the data encoding method based on the provided encoding_type."""
        encodings = {
            'raw': lambda data: data,  # raw/bytes
            'utf-8': lambda data: data.encode('utf-8'),
            'msgpack': lambda data: msgpack.packb(data, use_single_float=False, use_bin_type=True),
            'json': lambda data: orjson.dumps(data),
        }
        if encoding_type not in encodings:
            raise ValueError(f'Invalid encoding: {encoding_type}')
        self.encode = encodings[encoding_type]

    def publish(self, data: dict):
        """
        Publishes the provided data to the target URL.

        Parameters
        ----------
        data : dict
            Data to be published.
        """
        if self.is_enabled:
            converted_data = convert_to_python_builtin_types(data)
            encoded_data = self.encode(converted_data)
            self.socket.sendto(encoded_data, (self.hostname, self.url.port))


class DataReceiver:
    """
    Receives data published by a DataPublisher instance using a non-blocking socket.
    """

    def __init__(
        self, target_port: int = 9871, decoding_type: str = "msgpack"):
        """
        Initializes the DataReceiver.

        Args:
            target_port (int): The port to listen on for incoming data. Defaults to 9870.
            decoding_type (str): The decoding method for data ("msgpack" or "json"). Defaults to "msgpack".
        """   
        self.socket = socket.socket(socket.AF_INET, socket.SOCK_DGRAM)
        self.socket.setsockopt(socket.SOL_SOCKET, socket.SO_REUSEADDR, 1)
        self.socket.bind(("", target_port))
        self.socket.setblocking(False)
        decodings = {
            "raw": lambda data: data,  # raw/bytes
            "utf-8": lambda data: data.decode("utf-8"),
            "msgpack": lambda data: msgpack.unpackb(data, raw=False),
            "json": lambda data: orjson.loads(data),
        }
        if decoding_type not in decodings:
            raise ValueError(f"Invalid decoding: {decoding_type}")
        self.decode = decodings[decoding_type]
        self.data = None
        self.address = None
        self._running = True  # Flag to control the receive loop
        self.get_server_local_ip()
        self.get_server_public_ip()
        input('input to start')

    def receive(self, timeout=0.1, buffer_size=2048):
        """Receive and decode data from the socket if available, otherwise return None."""
        ready = select.select([self.socket], [], [], timeout)
        if ready[0]:
            data, self.address = self.socket.recvfrom(buffer_size)
            self.data = self.decode(data)
            # print(f"Received from {self.address}: {self.data}")
            return self.data, self.address  # Return decoded data and sender address
        else:
            return None, None  # No data received within the timeout

    def receive_continuously(self,timeout=0.1, buffer_size=2048):
        """Continuously receive and decode data from the socket in a dedicated thread."""

        def _receive_loop():
            while self._running:
                self.receive(timeout=timeout, buffer_size=buffer_size)

        thread = threading.Thread(target=_receive_loop, daemon=True)
        thread.start()

    def stop(self):
        """Stop continuous receiving."""
        self._running = False
        self.socket.close()
    def get_server_local_ip(verbose=True):
        local_ip = socket.gethostbyname(socket.gethostname())
        if verbose:
            print(f"#################"
                f"Server Local IP Address: {local_ip}"
                f"#################")
        return local_ip


    @staticmethod
    def get_server_public_ip(verbose=True):
        # Execute the hostname -I command and capture its output
        result = subprocess.run(['hostname', '-I'], capture_output=True, text=True)

        # Split the output by whitespace to get individual IP addresses
        ip_addresses = result.stdout.strip().split()
        
        # Check if there is a second IP address available
        if len(ip_addresses) > 0:
            if verbose:
                print(f"#################"
                    f"Server Public IP Address: {ip_addresses[-1]}"
                    f"#################")
            return ip_addresses[-1]  # Second IP address
        else:
            raise Exception("No Server Public IP address found; Please check your internet connection")

def convert_to_python_builtin_types(nested_data: dict):
    """
    Converts nested data (including tensors and arrays) to built-in types.

    Parameters
    ----------
    nested_data : dict
        Data to be converted.

    Returns
    -------
    dict
        Data converted to Python built-in types.
    """
    converted_data = {}
    for key, value in nested_data.items():
        if isinstance(value, dict):
            converted_data[key] = convert_to_python_builtin_types(value)
        elif isinstance(value, (torch.Tensor, np.ndarray)):
            converted_data[key] = value.tolist()
        else:
            converted_data[key] = value
    return converted_data

if __name__=="__main__":
    import time

    # Sample data to publish
    time_since_start = time.time()
    def test_data():
        """example test data"""
        return {"time":time.time()-time_since_start,"sensor_id": np.random.randint(0,10), "temperature": 25.5, "humidity": 68}

    # Create a publisher instance
    # publisher = DataPublisher(target_url="udp://localhost:9871", encoding_type="msgpack")

    # Create a receiver instance
    receiver = DataReceiver(target_port=9871, decoding_type="msgpack")

    # Start continuous receiving in a thread
    receiver.receive_continuously()
    init_speed = 200
    speed = 15
    i = 0

    # Gain should be adjusted to match simulation performance
    shoulder_gain = 1.5

    # Home the shoulders
    servo0.move(120,init_speed)
    servo1.move(120,init_speed)
    servo2.move(120, init_speed)
    servo3.move(120,init_speed)
    servo4.move(120,init_speed)
    servo5.move(120,init_speed)
    servo6.move(120,init_speed)
    servo7.move(120,init_speed)

    input()

    while True:
        # print(f"Received from {receiver.address}: {receiver.data}")

        if i == 0:
            time.sleep(1)
            i = i + 1

        angle = receiver.data['dof_pos']
        print(receiver.data)
        if angle is not None:
            
            angle_0 = shoulder_gain * np.degrees(angle[0]) + 120 # pos
            angle_1 = np.degrees(angle[1]) + 120 # pos
            angle_2 = shoulder_gain * np.degrees(angle[2]) + 120 # pos
            angle_3 = np.degrees(-1 * angle[3]) + 120
            angle_4 = shoulder_gain * np.degrees(-1 * angle[4]) + 120
            angle_5 = np.degrees(angle[5]) + 120 # pos
            angle_6 = shoulder_gain * np.degrees(-1 * angle[6]) + 120
            angle_7 = np.degrees(-1 * angle[7]) + 120

            servo0.move(angle_0, speed)
            servo1.move(angle_1, speed)
            servo2.move(angle_2, speed)
            servo3.move(angle_3, speed)
            servo4.move(angle_4, speed)
            servo5.move(angle_5, speed)
            servo6.move(angle_6, speed)
            servo7.move(angle_7, speed)

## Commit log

2024-06-24 init commit
    [A_bug_like_walking_robot_0514183118_preview.stl, A_quadrupedal_walking_robot_resembling_a_shoe_with_four_legs_0516130037_preview.stl, An_insect_like_walking_ro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]
2024-06-24 Start to clean repo
    [A_bug_like_walking_robot_0514183118_preview.stl, A_quadrupedal_walking_robot_resembling_a_shoe_with_four_legs_0516130037_preview.stl, An_insect_like_walking_ro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]
2024-06-24 Continue cleaning
    [A_bug_like_walking_robot_0514183118_preview.stl, A_quadrupedal_walking_robot_resembling_a_shoe_with_four_legs_0516130037_preview.stl, An_insect_like_walking_ro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]
2024-06-25 Added example frog bank, and better documentation on how to train and visualize bots
    [A_bug_like_walking_robot_0514183118_preview.stl, A_quadrupedal_walking_robot_resembling_a_shoe_with_four_legs_0516130037_preview.stl, An_insect_like_walking_ro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]
2024-06-28 Update README.md to include assembly instructions
